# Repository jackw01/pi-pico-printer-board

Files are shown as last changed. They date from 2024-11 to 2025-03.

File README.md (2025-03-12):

# pi-pico-printer-board

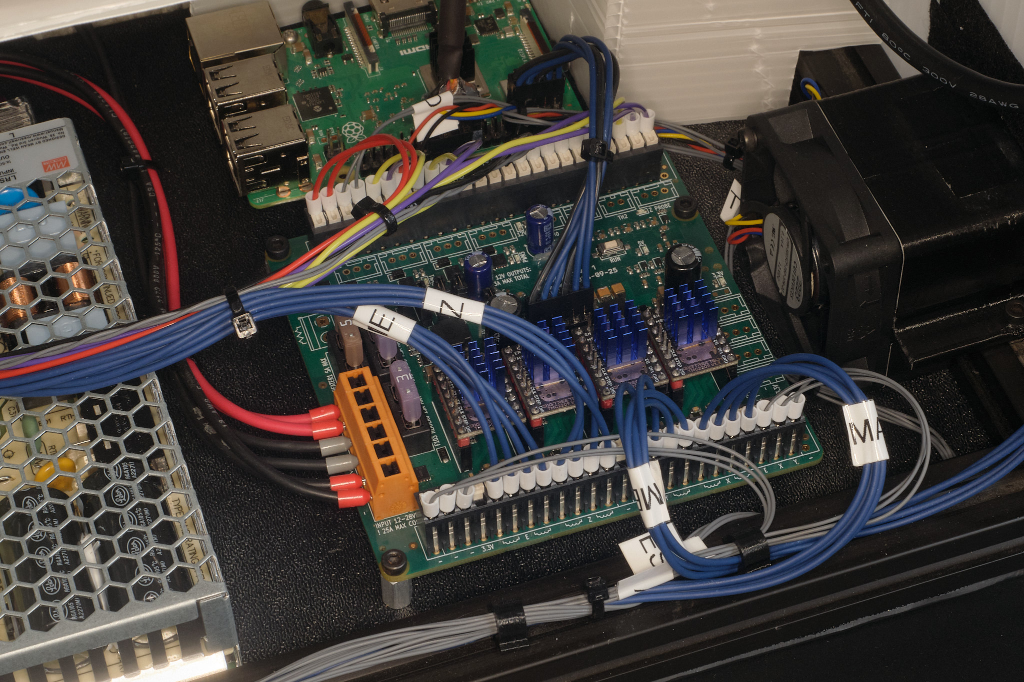
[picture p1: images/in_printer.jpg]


## features

* Klipper compatible
* Uses Raspberry Pi Pico (RP2040)
* High reliability Weidmüller push-in connectors for all inputs and outputs
* 20A max and 7.5A max separately fused heater outputs
* 4x 3A max general purpose PWM outputs, individually configurable for 12V or 24V power, capable of driving inductive loads
* 3x thermistor inputs with 2.4Kohm pull up resistors
* 4x endstop inputs with one configurable for 5V or 12V operation for Z-probe
* 4x motor driver sockets
* Onboard 12V 3A and 5V 3A buck converters for powering accessories including Raspberry Pi
* Compatible with both 12V and 24V systems; components rated for 28V
* Compatible with both TMC2209 and A4988 motor drivers, and possibly others
* ESD and short-to-Vin protection on all microcontroller inputs
* Motor driver ESD and coil overvoltage protection
* Indicator LEDs for all power rails and outputs
* Alternatively supports 2.54mm pitch (Molex SL), or 2.5mm pitch (JST SM) headers for all inputs and outputs
* Labeled PCB for ease of setup and tinkering
* Open source PCB design

## design

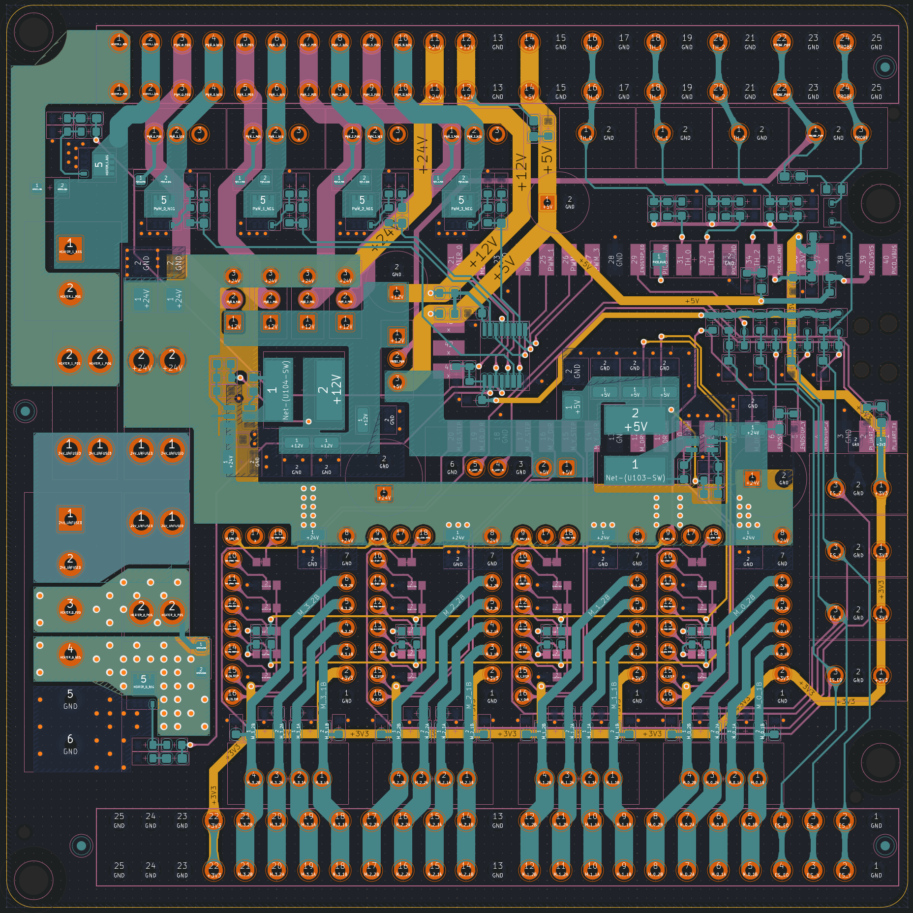
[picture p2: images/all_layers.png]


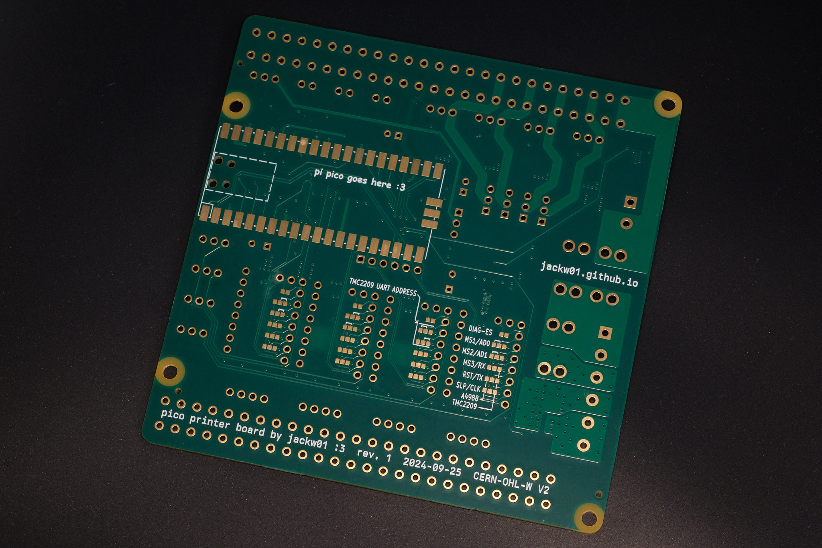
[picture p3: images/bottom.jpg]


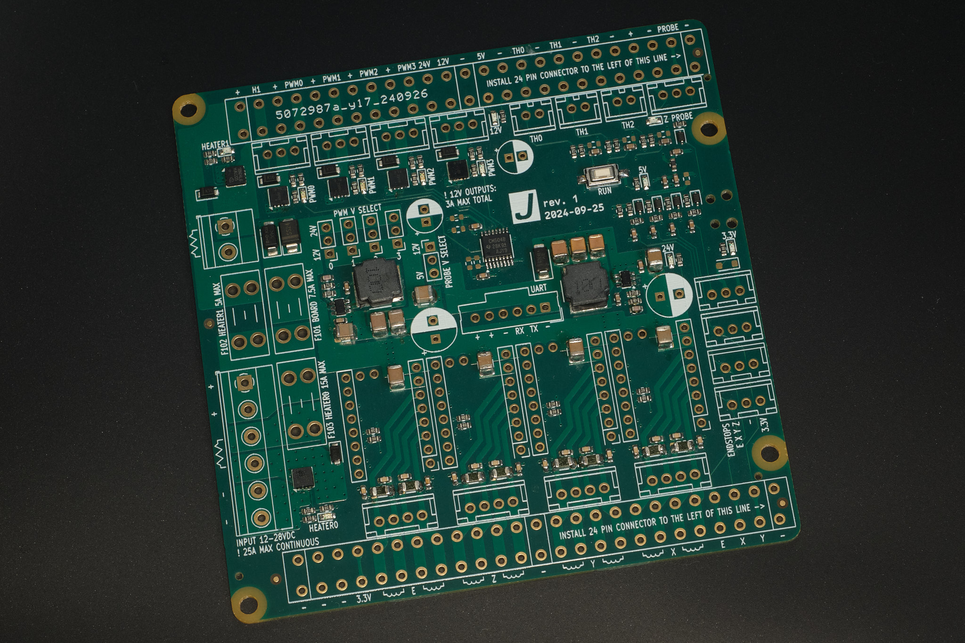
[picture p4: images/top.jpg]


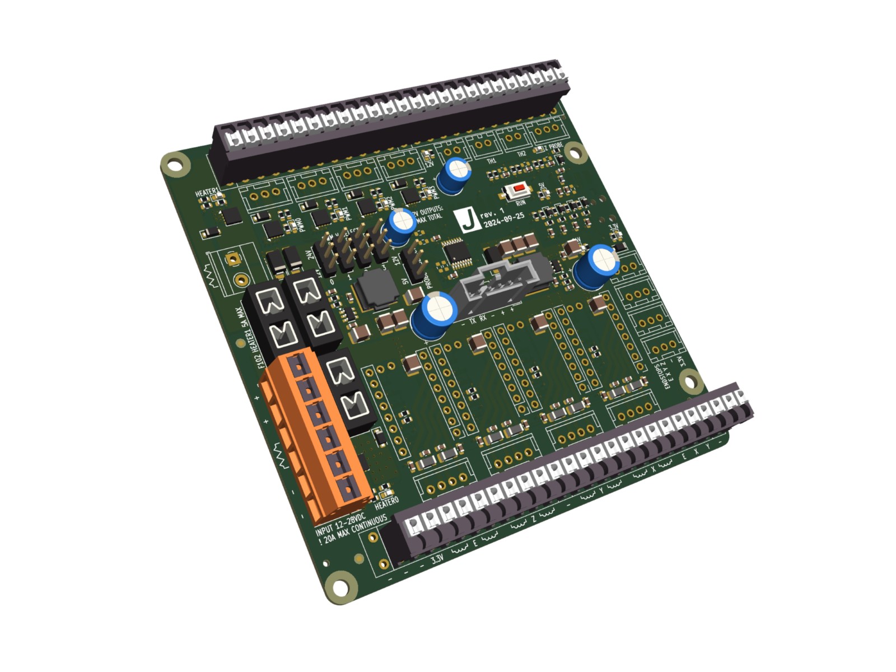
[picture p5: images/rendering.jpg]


[Schematic as PDF](pcb/rpi%20pico%20printer%20board%20rev1%2020241010.pdf)

[Sample Klipper Configuration File](klipper/printer.cfg)

[BOM (Excel)](pcb/bom.xlsx)

### license
This project is released under the CERN Open Hardware Licence Version 2 - Weakly Reciprocal (CERN-OHL-W V2).

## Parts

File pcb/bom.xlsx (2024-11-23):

 |  |  |  |  | 168 | 25 |  |  |  |  | $48.15 |  |  | $123.98
Reference | Value | Datasheet | Footprint | SMT | Qty | Qty THT | DNP | MPN | JLCPCB Basic/ExtPref | Cost | Ext. Cost Per Board | MOQ | Already Have? | Order Cost
A201,A301,A401,A501 | Stepper Driver Breakout | ~ | Custom:BTT_TMC2209_Breakout-16_15.2x20.3mm |  | 8 | 8 |  | RS1-08-G |  | 0.43 | 3.44 | 17 |  | 7.31
C101,C102,C104,C109,C116,C118,C125,C127,C128,C129,C130 | 0.1u | ~ | Capacitor_SMD:C_0603_1608Metric | Y | 11 | 0 |  | CL10B104KB8NNWC | CC0603KRX7R9BB104 | 0.0079 | 0.0869 | 100 |  | 0
C103,C105,C106,C108,C117 | 2.2u | ~ | Capacitor_SMD:C_0603_1608Metric | Y | 5 | 0 |  | CL10B225KP8NNNC | CL10A225KO8NNNC | 0.041 | 0.205 | 50 |  | 0
C107,C126 | 470u | ~ | Capacitor_THT:CP_Radial_D8.0mm_P3.50mm |  | 2 | 2 |  | EEU-FR1V471L |  | 0.451 | 0.902 | 10 |  | 4.51
C110 | 47p | ~ | Capacitor_SMD:C_0603_1608Metric | Y | 1 | 0 |  | CL10C470JB8NNNC | CL10C470JB8NNNC | 0.034 | 0.034 | 10 |  | 0
C111,C112,C113 | 22u | ~ | Capacitor_SMD:C_1210_3225Metric | Y | 3 | 0 |  | CL32B226KOJNNNE |  | 0.295 | 0.885 | 10 |  | 2.95
C114,C123 | 100u | ~ | Capacitor_THT:CP_Radial_D6.3mm_P2.50mm |  | 2 | 2 |  | ECA-1VM101 |  | 0.19 | 0.38 | 10 |  | 1.9
C115,C120,C121,C122,C124,C201,C301,C401,C501 | 10u | ~ | Capacitor_SMD:C_1210_3225Metric | Y | 9 | 0 |  | CL32B106KBJNNNE |  | 0.2806 | 2.5254 | 50 |  | 14.03
C119 | 12p | ~ | Capacitor_SMD:C_0603_1608Metric | Y | 1 | 0 |  | CL10C120JB8NNNC | CL10C120JB8NNNC | 0.022 | 0.022 | 10 |  | 0
C203,C204,C205,C206,C303,C304,C305,C306,C403,C404,C405,C406,C503,C504,C505,C506 | 1n | ~ | Capacitor_SMD:C_0603_1608Metric | Y | 16 | 0 |  | CL10B102KB8NNNC | CL10B102KB8NNNC | 0.0122 | 0.1952 | 100 |  | 0
D101,D102,D106,D107,D108,D112,D113,D114,D118,D120,D123 | LED | ~ | LED_SMD:LED_0603_1608Metric_Pad1.05x0.95mm_HandSolder | Y | 11 | 0 |  | B1911UD--20D001014U1930 | KT-0603R | 0.047 | 0.517 | 10 |  | 0
D103,D104,D105,D109,D110,D111 | DSS16U | ~ | Diode_SMD:D_SOD-123 | Y | 6 | 0 |  | DSS16U | DSK16 | 0.119 | 0.714 | 10 |  | 0
D115 | D3V3AP2W | ~ | Diode_SMD:D_SOD-123 | Y | 1 | 0 |  | GSMF3.3CA |  | 0.134 | 0.134 | 10 |  | 1.34
D116 | SMAJ30A | ~ | Diode_SMD:D_SMA | Y | 1 | 0 |  | SMAJ30A | SMAJ30CA | 0.39 | 0.39 | 1 |  | 0
D117 | SMAJ5.0A | ~ | Diode_SMD:D_SMA | Y | 1 | 0 |  | SMAJ5.0A | SMAJ5.0A | 0.39 | 0.39 | 1 |  | 0
D119,D121,D122,D124,D125 | BAT46WS | ~ | Diode_SMD:D_SOD-323 | Y | 5 | 0 |  | BAT46WS | BAT46WS | 0.139 | 0.695 | 10 |  | 0
D126 | SS24 | ~ | Diode_SMD:D_SMA | Y | 1 | 0 |  | SS24 | SS24 | 0.267 | 0.267 | 10 |  | 0
F101 | 5A | ~ | Fuse:Fuseholder_Blade_Mini_Keystone_3568 |  | 1 | 1 |  | 3568 |  | 1.31 | 1.31 | 1 |  | 2.62
F102 | 7.5A | ~ | Fuse:Fuseholder_Blade_Mini_Keystone_3568 |  | 1 | 1 |  | 3568 |  | 1.31 | 1.31 | 1 |  | 2.62
F103 | 15A | ~ | Fuse:Fuseholder_Blade_Mini_Keystone_3568 |  | 1 | 1 |  | 3568 |  | 1.31 | 1.31 | 1 |  | 2.62
FB101 | 600ohm@100MHz | ~ | Inductor_SMD:L_0603_1608Metric | Y | 1 | 0 |  | BLM18AG601SH1D | GZ1608D601TF | 0.071 | 0.071 | 10 |  | 0
J101,J102,J105,J106,J120 | 2.54mm | ~ | Connector_PinHeader_2.54mm:PinHeader_1x03_P2.54mm_Vertical |  | 5 | 5 |  | PH1-03-UA |  | 0.047 | 0.235 | 10 |  | 0.47
J109,J110 | Conn_01x25 | ~ | Custom:Weidmuller_1870890000_25 |  | 2 | 2 |  | 1870630000 |  | 5.55 | 11.1 | 1 |  | 22.2
J113 | UART | ~ | Custom:Molex_SL_171971-0006_1x06_P2.54mm_Vertical |  | 1 | 1 |  | 1719710006 |  | 1.43 | 1.43 | 1 |  | 2.86
J114 | Screw_Terminal_01x06 | ~ | Custom:Weidmuller_LMFV_5.00_06_90 |  | 1 | 1 |  | 2786570000 |  | 4.26 | 4.26 | 1 |  | 8.52
L101,L102 | 10uH | ~ | Custom:L_Bourns_SRN8040TA | Y | 2 | 0 |  | SRN8040TA-100M |  | 0.552 | 1.104 | 10 |  | 5.52
Q101,Q104 | BSZ021N04 |  | Package_SON:Diodes_PowerDI3333-8 | Y | 2 | 0 |  | BSZ021N04LS6ATMA1 |  | 1.566 | 3.132 | 10 |  | 15.66
Q102,Q103,Q105,Q106 | DMT4011LFG |  | Package_SON:Diodes_PowerDI3333-8 | Y | 4 | 0 |  | DMT4011LFG-13 |  | 0.442 | 1.768 | 10 |  | 4.42
R101,R109,R110,R111,R119,R120,R121 | 22k | ~ | Resistor_SMD:R_0603_1608Metric | Y | 7 | 0 |  |  | 0603WAF2202T5E | 0.0078 | 0.0546 | 50 |  | 0
R102,R125,R129,R137 | 2.49k | ~ | Resistor_SMD:R_0603_1608Metric | Y | 4 | 0 |  |  | 0603WAF2401T5E | 0.0078 | 0.0312 | 50 |  | 0
R104,R112,R113,R114,R122,R123,R124,R126,R128,R130,R131,R132,R134,R135,R136,R139,R140,R141,R145,R149 | 10k | ~ | Resistor_SMD:R_0603_1608Metric | Y | 20 | 0 |  |  | 0603WAF1002T5E | 0.0078 | 0.156 | 50 |  | 0
R105,R106,R107,R116,R117,R118,R150,R202,R302,R402,R502 | 1k | ~ | Resistor_SMD:R_0603_1608Metric | Y | 11 | 0 |  |  | 0603WAF1001T5E | 0.0078 | 0.0858 | 50 |  | 0
R138 | 172k | ~ | Resistor_SMD:R_0603_1608Metric | Y | 1 | 0 |  |  | 0603WAF1803T5E | 0.0078 | 0.0078 | 50 |  | 0
R143,R146 | 31.6k | ~ | Resistor_SMD:R_0603_1608Metric | Y | 2 | 0 |  |  | 0603WAF3302T5E | 0.0078 | 0.0156 | 50 |  | 0
R144 | 475k | ~ | Resistor_SMD:R_0603_1608Metric | Y | 1 | 0 |  |  | 0603WAF4703T5E | 0.0078 | 0.0078 | 50 |  | 0
R201,R301,R401,R501 | 100 | ~ | Resistor_SMD:R_0603_1608Metric | Y | 4 | 0 |  |  | 0603WAF1000T5E | 0.0078 | 0.0312 | 50 |  | 0
RV201,RV202,RV301,RV302,RV401,RV402,RV501,RV502 | 26V | ~ | Inductor_SMD:L_1206_3216Metric | Y | 8 | 0 |  | ZV25K1206201NIR1 |  | 0.298 | 2.384 | 25 |  | 7.45
SW101 | PTS636 SM25 SMTR LFS | ~ | Button_Switch_SMD:SW_SPST_CK_RS282G05A3 | Y | 1 | 0 |  | PTS636 SM25 SMTR LFS |  | 0.24 | 0.24 | 1 |  | 0.48
U101 | 4504 | ~ | Package_SO:TSSOP-16_4.4x5mm_P0.65mm | Y | 1 | 0 |  | CD4504BPWR |  | 0.482 | 0.482 | 10 |  | 4.82
U102 | Raspberry Pi Pico | ~ | Custom:RPi_Pico_SMD_minimal |  | 1 | 1 |  | SC0915 |  | 4 | 4 | 1 |  | 8
U103,U104 | AP63300WU | https://www.diodes.com/assets/Datasheets/AP63300-AP63301.pdf | Package_TO_SOT_SMD:TSOT-23-6 | Y | 2 | 0 |  | AP63300WU-7 |  | 0.92 | 1.84 | 1 |  | 3.68

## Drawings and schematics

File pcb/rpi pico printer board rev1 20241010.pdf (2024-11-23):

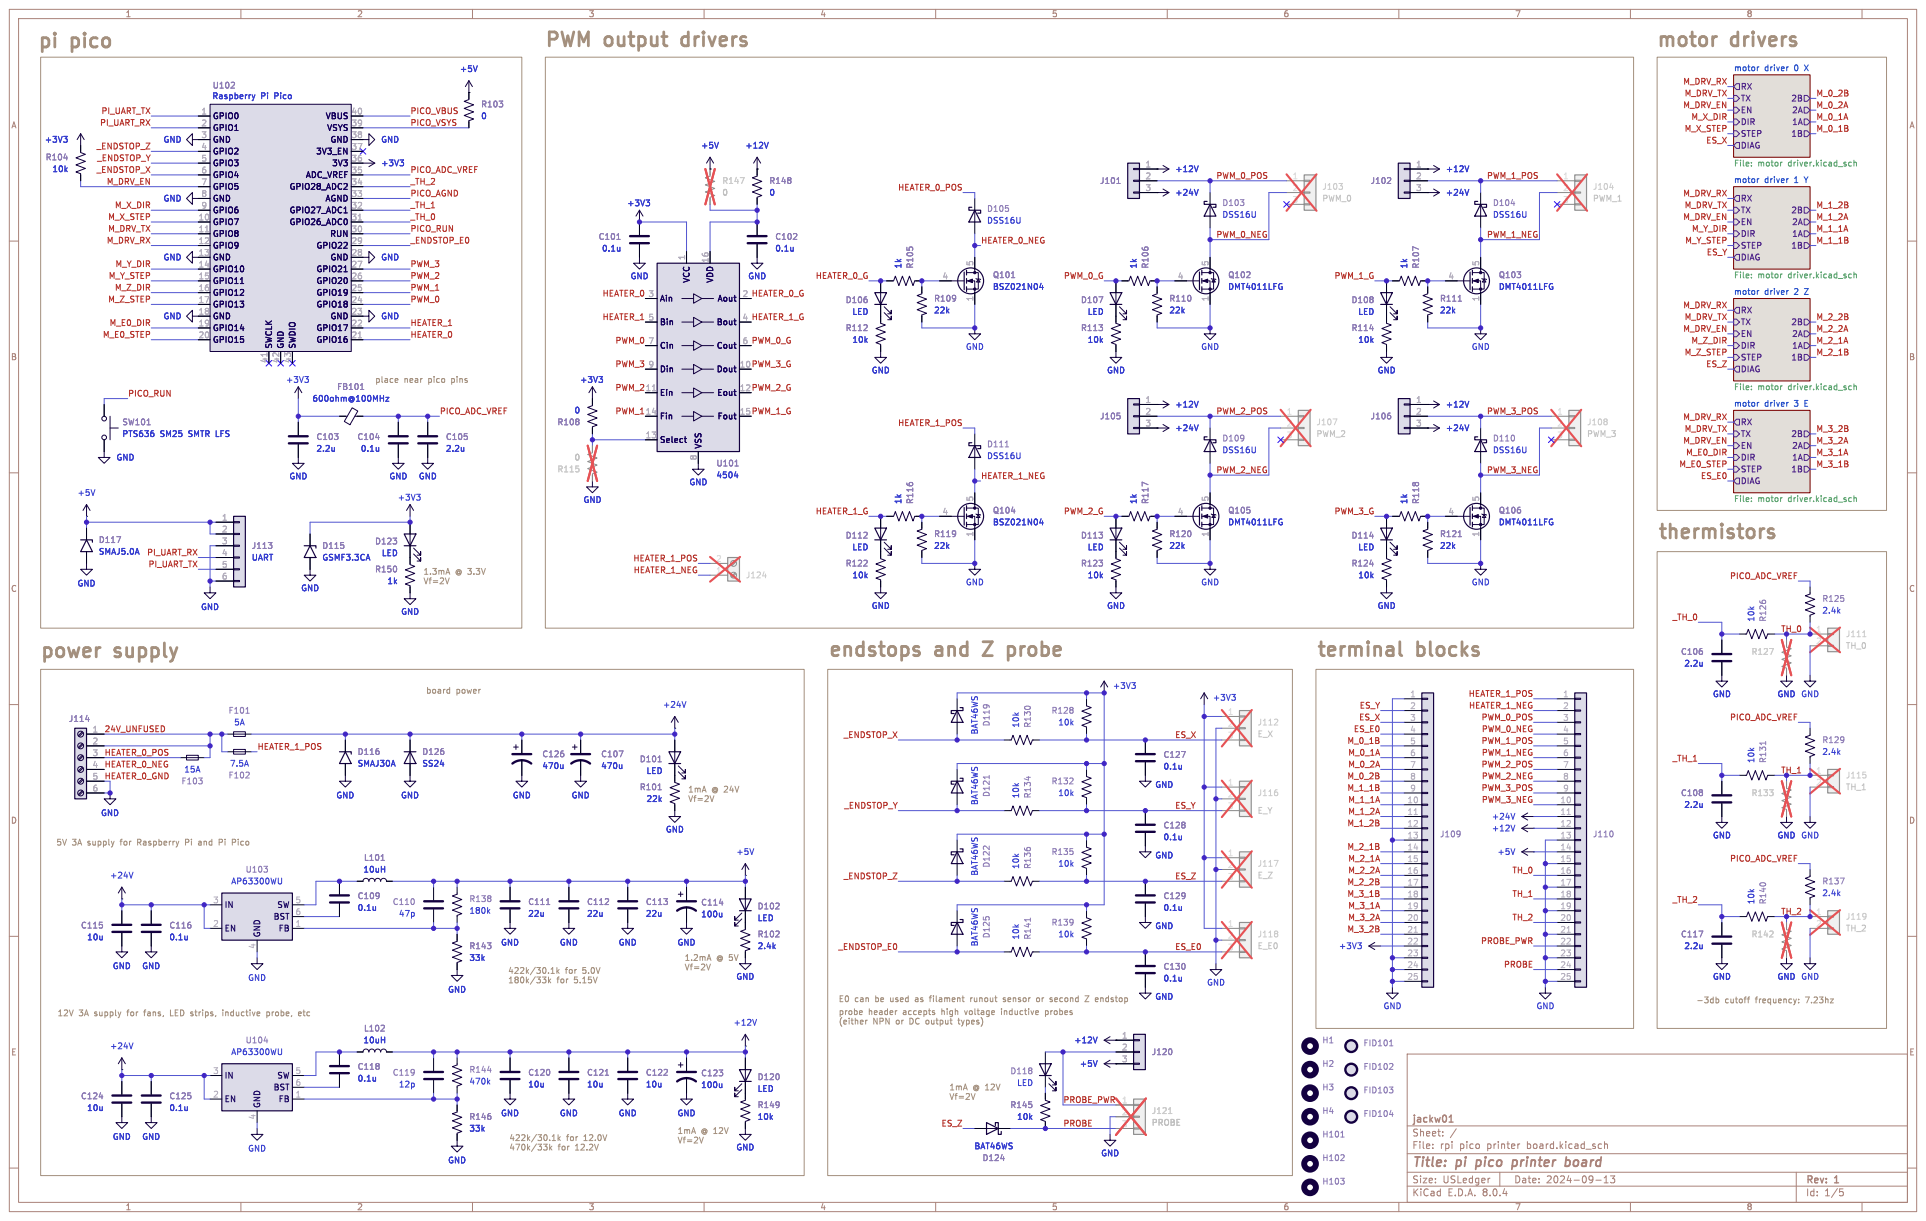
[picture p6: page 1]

STEP
DIAG
File: motor driver.kicad_sch DIR
2B motor driver 2 Z

1 Dout 10 Ein 11 Eout 12 Select 13 Fin 14 Fout 15 VDD 16 Aout 2 Ain 3 Bout 4 Bin 5 Cout 6 Cin 7 VSS
GND

2B motor driver 3 E

place near pico pins

5V 3A supply for Raspberry Pi and Pi Pico

(either NPN or DC output types)

jackw01
Id: 1/5 Title: pi pico printer board

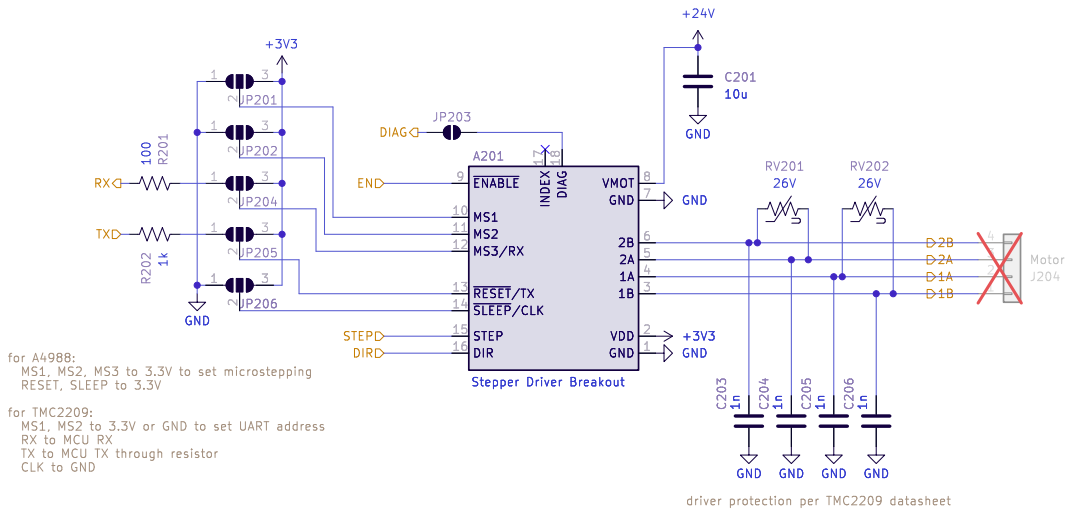
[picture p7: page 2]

J204 Motor +3V3 GND GND GND

for A4988: MS1, MS2, MS3 to 3.3V to set microstepping RESET, SLEEP to 3.3V

for TMC2209: MS1, MS2 to 3.3V or GND to set UART address RX to MCU RX

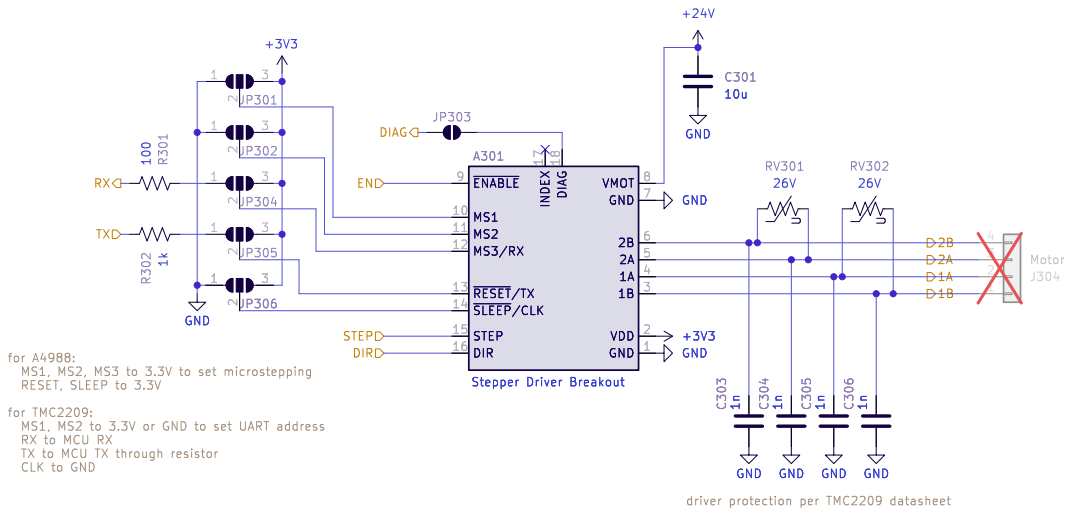
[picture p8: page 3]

for A4988: MS1, MS2, MS3 to 3.3V to set microstepping RESET, SLEEP to 3.3V

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

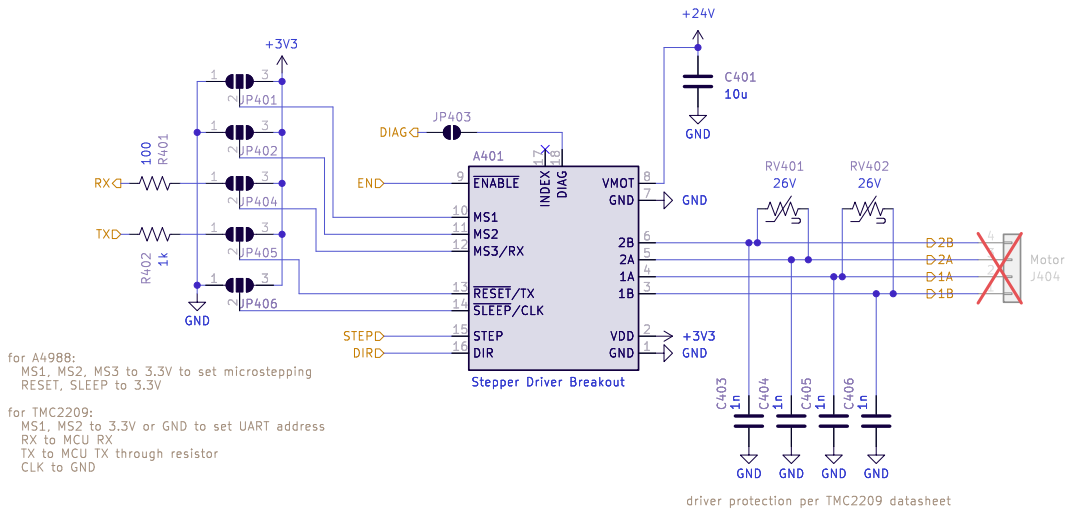
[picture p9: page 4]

for A4988: MS1, MS2, MS3 to 3.3V to set microstepping RESET, SLEEP to 3.3V

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

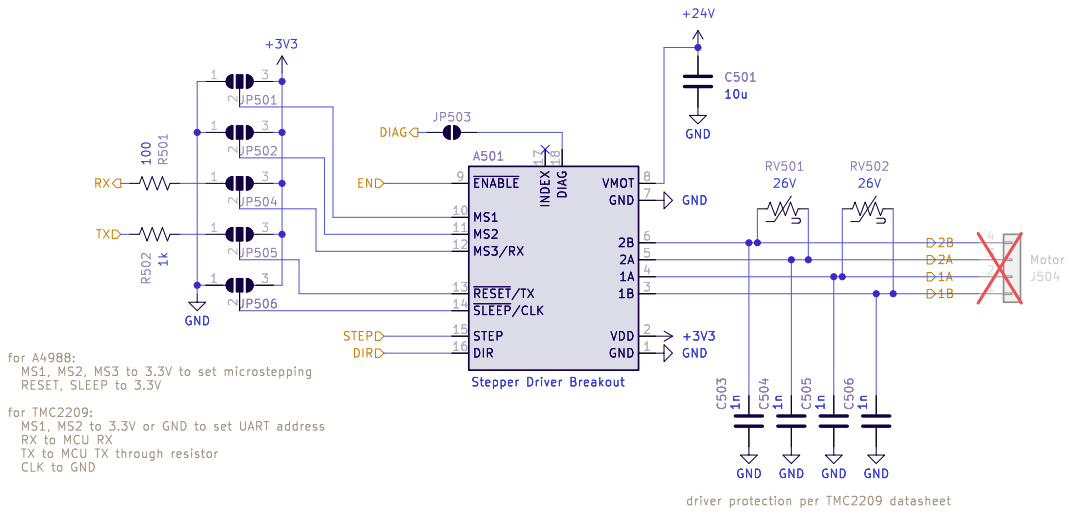
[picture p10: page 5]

J504 Motor +3V3 GND GND GND

for A4988: MS1, MS2, MS3 to 3.3V to set microstepping RESET, SLEEP to 3.3V

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

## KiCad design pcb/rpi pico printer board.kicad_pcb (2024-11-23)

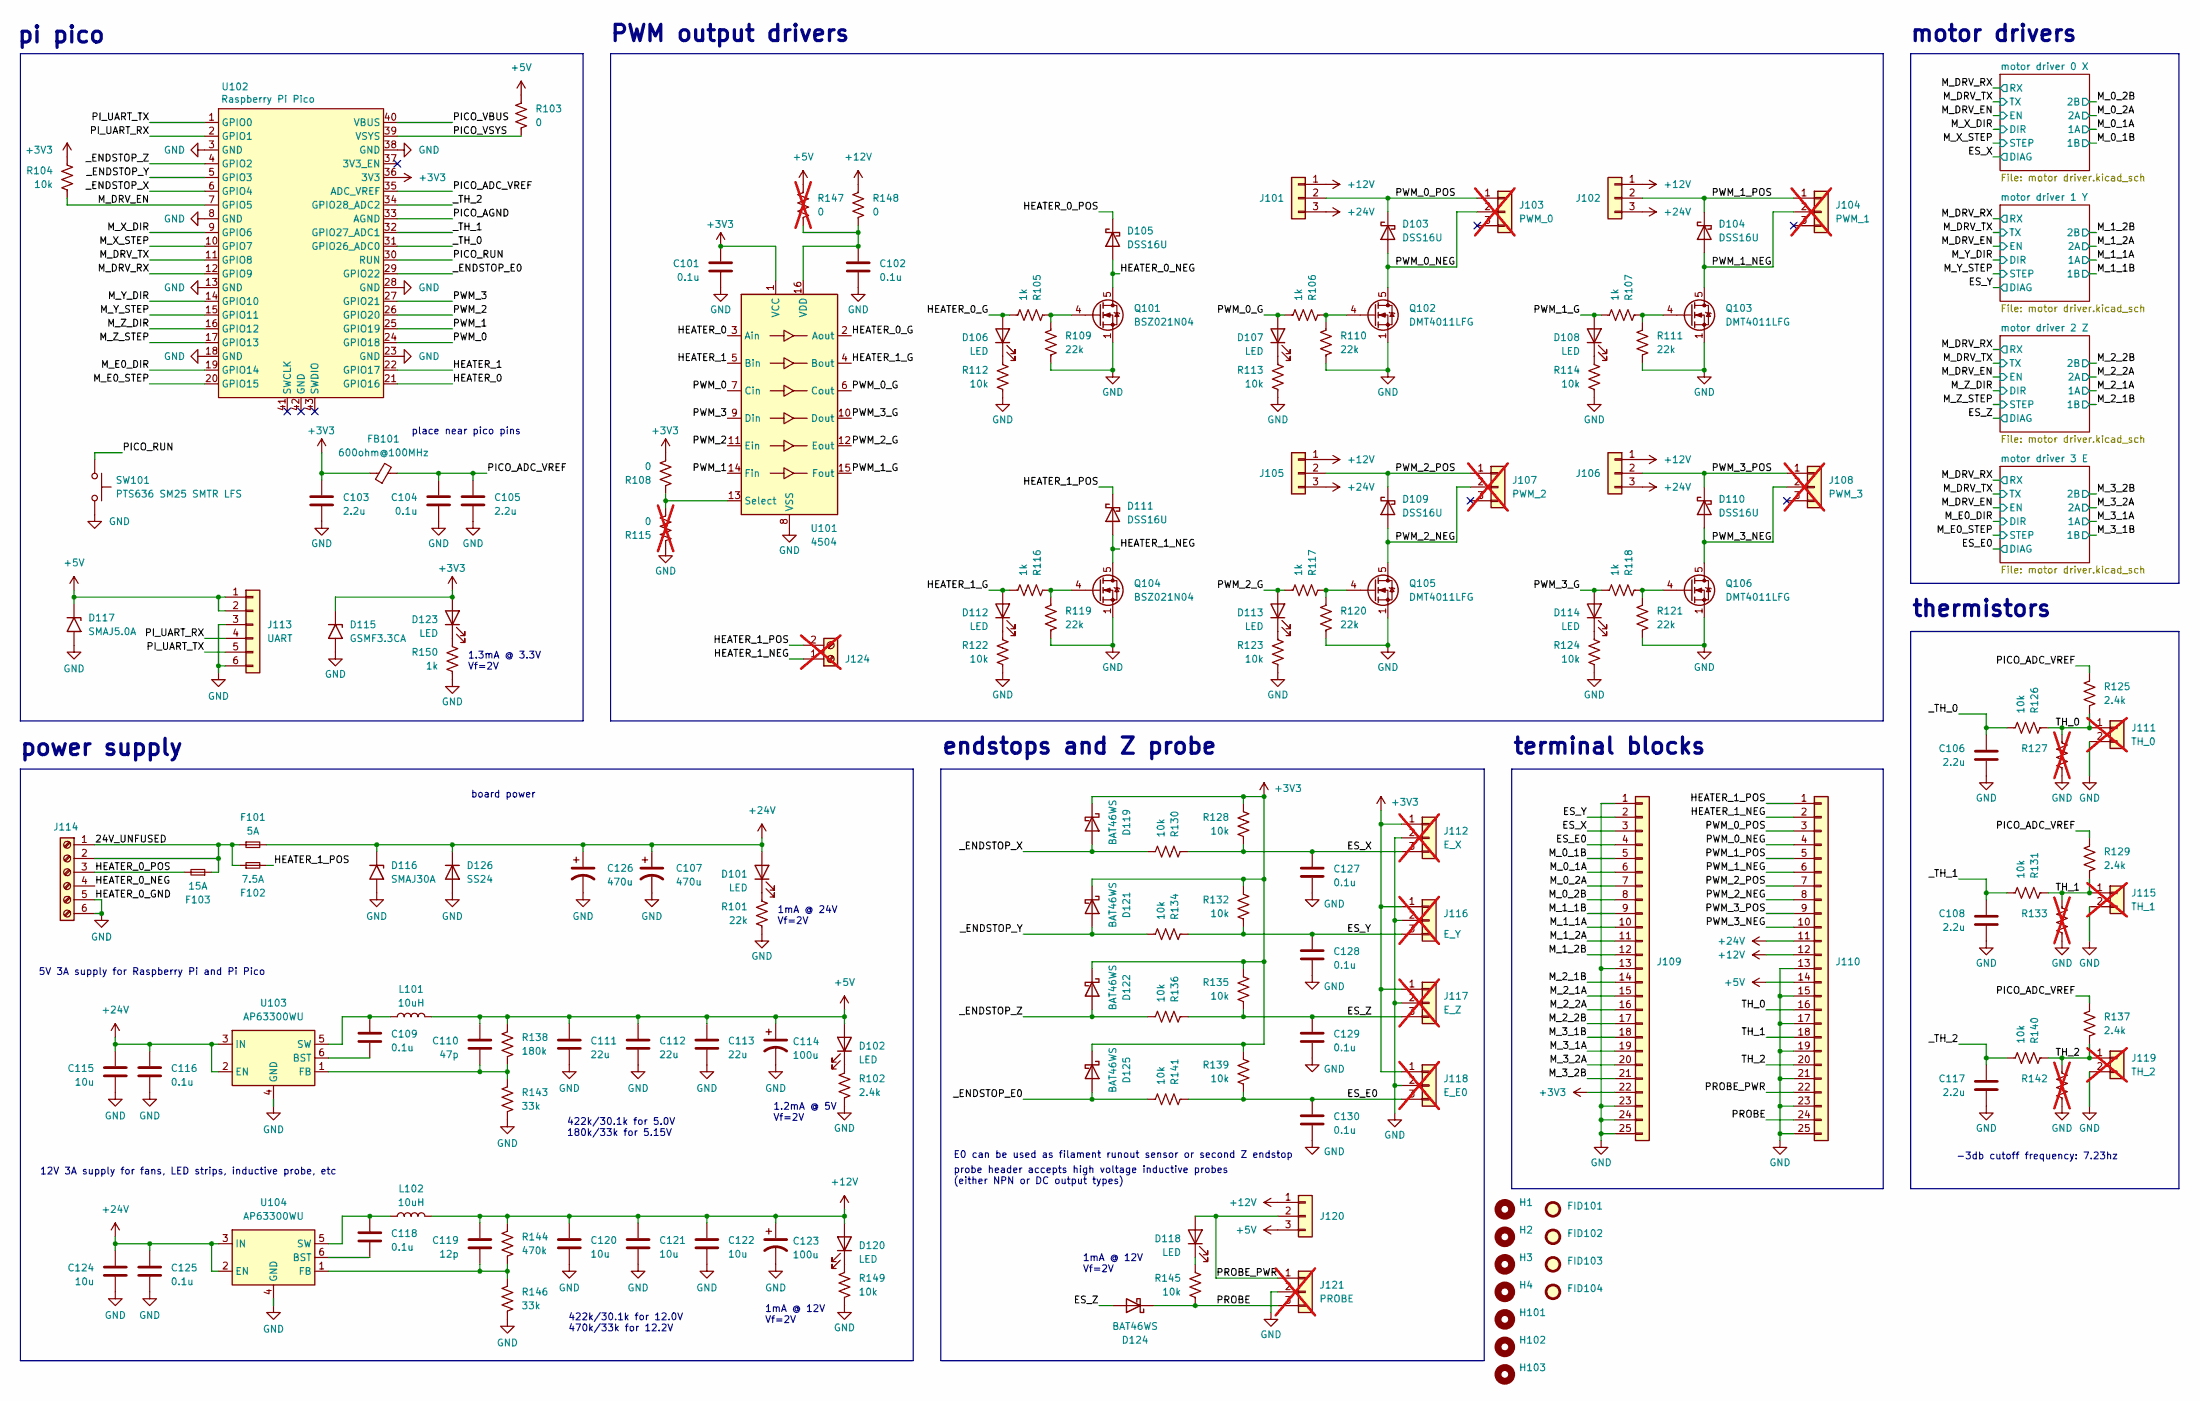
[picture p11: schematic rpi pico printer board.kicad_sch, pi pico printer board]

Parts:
C101, C102, C104, C109, C116, C118, C125, C127, C128, C129, C130: 0.1u; C_0603_1608Metric; MPN CL10B104KB8NNWC; JLCPCB Basic Part CC0603KRX7R9BB104
C103, C105, C106, C108, C117: 2.2u; C_0603_1608Metric; MPN CL10B225KP8NNNC; JLCPCB Basic Part CL10A225KO8NNNC
C107, C126: 470u; CP_Radial_D8.0mm_P3.50mm; MPN EEU-FR1V471L
C110: 47p; C_0603_1608Metric; MPN CL10C470JB8NNNC; JLCPCB Basic Part CL10C470JB8NNNC
C111, C112, C113: 22u; C_1210_3225Metric; MPN CL32B226KOJNNNE
C114, C123: 100u; CP_Radial_D6.3mm_P2.50mm; MPN ECA-1VM101
C115, C120, C121, C122, C124: 10u; C_1210_3225Metric; MPN CL32B106KBJNNNE
C119: 12p; C_0603_1608Metric; MPN CL10C120JB8NNNC; JLCPCB Basic Part CL10C120JB8NNNC
D101, D102, D106, D107, D108, D112, D113, D114, D118, D120, D123: LED; LED_0603_1608Metric_Pad1.05x0.95mm_HandSolder; MPN B1911UD--20D001014U1930; JLCPCB Basic Part KT-0603R
D103, D104, D105, D109, D110, D111: DSS16U; D_SOD-123F; MPN DSS16U; JLCPCB Basic Part DSK16
D115: GSMF3.3CA; D_SOD-123F; MPN GSMF3.3CA; JLCPCB Basic Part SMF3.3CA
D116: SMAJ30A; D_SMA; MPN SMAJ30A; JLCPCB Basic Part SMAJ30CA
D117: SMAJ5.0A; D_SMA; MPN SMAJ5.0A; JLCPCB Basic Part SMAJ5.0A
D119, D121, D122, D124, D125: BAT46WS; D_SOD-323; MPN BAT46WS; JLCPCB Basic Part BAT46WS
D126: SS24; D_SMA; MPN SS24; JLCPCB Basic Part SS24
F101: 5A; Fuseholder_Blade_Mini_Keystone_3568; MPN 3568
F102: 7.5A; Fuseholder_Blade_Mini_Keystone_3568; MPN 3568
F103: 15A; Fuseholder_Blade_Mini_Keystone_3568; MPN 3568
FB101: 600ohm@100MHz; L_0603_1608Metric; MPN BLM18AG601SH1D; JLCPCB Basic Part GZ1608D601TF
FID101, FID102, FID103, FID104: Fiducial_1mm_Mask2mm
H1, H2, H3, H4: MountingHole; MountingHole_3.2mm_M3_Mask
H101, H102, H103: ToolingHole; JLC_tooling_hole
J101, J102, J105, J106, J120: 2.54mm; PinHeader_1x03_P2.54mm_Vertical; MPN PH1-03-UA
J103: PWM_0; JST_XH_plus_2.54mm_01x03; not fitted
J104: PWM_1; JST_XH_plus_2.54mm_01x03; not fitted
J107: PWM_2; JST_XH_plus_2.54mm_01x03; not fitted
J108: PWM_3; JST_XH_plus_2.54mm_01x03; not fitted
J109, J110: Conn_01x25; Weidmuller_1870890000_25; MPN 1870630000
J111: TH_0; JST_XH_plus_2.54mm_01x02; not fitted
J112: E_X; JST_XH_plus_2.54mm_01x03; not fitted
J113: UART; Molex_SL_171971-0006_1x06_P2.54mm_Vertical; MPN 1719710006
J114: Screw_Terminal_01x06; Weidmuller_LMFV_5.00_06_90; MPN 2786570000
J115: TH_1; JST_XH_plus_2.54mm_01x02; not fitted
J116: E_Y; JST_XH_plus_2.54mm_01x03; not fitted
J117: E_Z; JST_XH_plus_2.54mm_01x03; not fitted
J118: E_E0; JST_XH_plus_2.54mm_01x03; not fitted
J119: TH_2; JST_XH_plus_2.54mm_01x02; not fitted
J121: PROBE; JST_XH_plus_2.54mm_01x03; not fitted
J124: Screw_Terminal_01x02; TerminalBlock_Phoenix_MKDS-1,5-2_1x02_P5.00mm_Horizontal; not fitted
L101, L102: 10uH; L_Bourns_SRN8040TA; MPN SRN8040TA-100M
Q101, Q104: BSZ021N04; Diodes_PowerDI3333-8; MPN BSZ021N04LS6ATMA1
Q102, Q103, Q105, Q106: DMT4011LFG; Diodes_PowerDI3333-8; MPN DMT4011LFG-13
R101, R109, R110, R111, R119, R120, R121: 22k; R_0603_1608Metric; JLCPCB Basic Part 0603WAF2202T5E
R102, R125, R129, R137: 2.4k; R_0603_1608Metric; JLCPCB Basic Part 0603WAF2401T5E
R103, R108, R148: 0; R_0603_1608Metric_Bridged
R104, R112, R113, R114, R122, R123, R124, R126, R128, R130, R131, R132, R134, R135, R136, R139, R140, R141, R145, R149: 10k; R_0603_1608Metric; JLCPCB Basic Part 0603WAF1002T5E
R105, R106, R107, R116, R117, R118, R150: 1k; R_0603_1608Metric; JLCPCB Basic Part 0603WAF1001T5E
R115, R147: 0; R_0603_1608Metric; not fitted
R127, R133, R142: R_0603_1608Metric; not fitted
R138: 180k; R_0603_1608Metric; JLCPCB Basic Part 0603WAF1803T5E
R143, R146: 33k; R_0603_1608Metric; JLCPCB Basic Part 0603WAF3302T5E
R144: 470k; R_0603_1608Metric; JLCPCB Basic Part 0603WAF4703T5E
SW101: PTS636 SM25 SMTR LFS; SW_SPST_CK_RS282G05A3; MPN PTS636 SM25 SMTR LFS
U101: 4504; TSSOP-16_4.4x5mm_P0.65mm; MPN CD4504BPWR
U102: Raspberry Pi Pico; RPi_Pico_SMD_minimal; MPN SC0915
U103, U104: AP63300WU; TSOT-23-6; MPN AP63300WU-7

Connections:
+3V3: C101.1, C103.1, D115.1 (A1), D119.1 (K), D121.1 (K), D122.1 (K), D123.2 (A), D125.1 (K), FB101.1, J109.22, J112.1, J116.1, J117.1, J118.1, R104.1, R108.2, R128.1, R132.1, R135.1, R139.1, U101.1 (VCC), U102.36 (3V3); also elsewhere on the board
+5V: C110.1, C111.1, C112.1, C113.1, C114.1, D102.2 (A), D117.1 (A1), J110.14, J113.1, J113.2, J120.3, L101.2, R103.1, R138.1, R147.1
+12V: C119.1, C120.1, C121.1, C122.1, C123.1, D120.2 (A), J101.1, J102.1, J105.1, J106.1, J110.12, J120.1, L102.2, R144.1, R148.1
+24V: C107.1, C115.1, C116.1, C124.1, C125.1, C126.1, D101.2 (A), D116.1 (A1), D126.1 (K), F101.2, J101.3, J102.3, J105.3, J106.3, J110.11, U103.2 (EN), U103.3 (IN), U104.2 (EN), U104.3 (IN); also elsewhere on the board
/24V_UNFUSED: F101.1, F102.1, F103.1, J114.1, J114.2
/ES_E0: C130.1, J109.4, J118.3, R139.2, R141.1; also elsewhere on the board
/ES_X: C127.1, J109.3, J112.3, R128.2, R130.1; also elsewhere on the board
/ES_Y: C128.1, J109.2, J116.3, R132.2, R134.1; also elsewhere on the board
/ES_Z: C129.1, D124.2 (A), J117.3, R135.2, R136.1; also elsewhere on the board
/HEATER_0: U101.3 (Ain), U102.21 (GPIO16)
/HEATER_0_G: D106.2 (A), R105.2, U101.2 (Aout)
/HEATER_0_NEG: D105.2 (A), J114.4, Q101.5 (D)
/HEATER_0_POS: D105.1 (K), F103.2, J114.3
/HEATER_1: U101.5 (Bin), U102.22 (GPIO17)
/HEATER_1_G: D112.2 (A), R116.2, U101.4 (Bout)
/HEATER_1_NEG: D111.2 (A), J110.2, J124.1, Q104.5 (D)
/HEATER_1_POS: D111.1 (K), F102.2, J110.1, J124.2
/M_0_1A: J109.6; also elsewhere on the board
/M_0_1B: J109.5; also elsewhere on the board
/M_0_2A: J109.7; also elsewhere on the board
/M_0_2B: J109.8; also elsewhere on the board
/M_1_1A: J109.10; also elsewhere on the board
/M_1_1B: J109.9; also elsewhere on the board
/M_1_2A: J109.11; also elsewhere on the board
/M_1_2B: J109.12; also elsewhere on the board
/M_2_1A: J109.15; also elsewhere on the board
/M_2_1B: J109.14; also elsewhere on the board
/M_2_2A: J109.16; also elsewhere on the board
/M_2_2B: J109.17; also elsewhere on the board
/M_3_1A: J109.19; also elsewhere on the board
/M_3_1B: J109.18; also elsewhere on the board
/M_3_2A: J109.20; also elsewhere on the board
/M_3_2B: J109.21; also elsewhere on the board
/M_DRV_EN: R104.2, U102.7 (GPIO5); also elsewhere on the board
/M_DRV_RX: U102.12 (GPIO9); also elsewhere on the board
/M_DRV_TX: U102.11 (GPIO8); also elsewhere on the board
/M_E0_DIR: U102.19 (GPIO14); also elsewhere on the board
/M_E0_STEP: U102.20 (GPIO15); also elsewhere on the board
/M_X_DIR: U102.9 (GPIO6); also elsewhere on the board
/M_X_STEP: U102.10 (GPIO7); also elsewhere on the board
/M_Y_DIR: U102.14 (GPIO10); also elsewhere on the board
/M_Y_STEP: U102.15 (GPIO11); also elsewhere on the board
/M_Z_DIR: U102.16 (GPIO12); also elsewhere on the board
/M_Z_STEP: U102.17 (GPIO13); also elsewhere on the board
/PICO_ADC_VREF: C104.1, C105.1, FB101.2, R125.1, R129.1, R137.1, U102.35 (ADC_VREF)
/PICO_AGND: U102.33 (AGND)
/PICO_RUN: SW101.1, U102.30 (RUN)
/PICO_VBUS: U102.40 (VBUS)
/PICO_VSYS: R103.2, U102.39 (VSYS)
/PI_UART_RX: J113.4, U102.2 (GPIO1)
/PI_UART_TX: J113.5, U102.1 (GPIO0)
/PROBE: D124.1 (K), J110.24, J121.3, R145.2
/PROBE_PWR: D118.2 (A), J110.22, J120.2, J121.1
/PWM_0: U101.7 (Cin), U102.24 (GPIO18)
/PWM_0_G: D107.2 (A), R106.2, U101.6 (Cout)
/PWM_0_NEG: D103.2 (A), J103.2, J110.4, Q102.5 (D)
/PWM_0_POS: D103.1 (K), J101.2, J103.1, J110.3
/PWM_1: U101.14 (Fin), U102.25 (GPIO19)
/PWM_1_G: D108.2 (A), R107.2, U101.15 (Fout)
/PWM_1_NEG: D104.2 (A), J104.2, J110.6, Q103.5 (D)
/PWM_1_POS: D104.1 (K), J102.2, J104.1, J110.5
/PWM_2: U101.11 (Ein), U102.26 (GPIO20)
/PWM_2_G: D113.2 (A), R117.2, U101.12 (Eout)
/PWM_2_NEG: D109.2 (A), J107.2, J110.8, Q105.5 (D)
/PWM_2_POS: D109.1 (K), J105.2, J107.1, J110.7
/PWM_3: U101.9 (Din), U102.27 (GPIO21)
/PWM_3_G: D114.2 (A), R118.2, U101.10 (Dout)
/PWM_3_NEG: D110.2 (A), J108.2, J110.10, Q106.5 (D)
/PWM_3_POS: D110.1 (K), J106.2, J108.1, J110.9
/TH_0: J110.16, J111.1, R125.2, R126.1, R127.1
/TH_1: J110.18, J115.1, R129.2, R131.1, R133.1
/TH_2: J110.20, J119.1, R137.2, R140.1, R142.1
/_ENDSTOP_E0: D125.2 (A), R141.2, U102.29 (GPIO22)
/_ENDSTOP_X: D119.2 (A), R130.2, U102.6 (GPIO4)
/_ENDSTOP_Y: D121.2 (A), R134.2, U102.5 (GPIO3)
/_ENDSTOP_Z: D122.2 (A), R136.2, U102.4 (GPIO2)
/_TH_0: C106.1, R126.2, U102.31 (GPIO26_ADC0)
/_TH_1: C108.1, R131.2, U102.32 (GPIO27_ADC1)
/_TH_2: C117.1, R140.2, U102.34 (GPIO28_ADC2)
GND: C101.2, C102.2, C103.2, C104.2, C105.2, C106.2, C107.2, C108.2, C111.2, C112.2, C113.2, C114.2, C115.2, C116.2, C117.2, C120.2, C121.2, C122.2, C123.2, C124.2, C125.2, C126.2, C127.2, C128.2, C129.2, C130.2, D115.2 (A2), D116.2 (A2), D117.2 (A2), D126.2 (A), J109.1, J109.13, J109.23, J109.24, J109.25, J110.13, J110.15, J110.17, J110.19, J110.21, J110.23, J110.25, J111.2, J112.2, J113.3, J113.6, J114.5, J114.6, J115.2, J116.2, J117.2, J118.2, J119.2, J121.2, Q101.1 (S), Q101.2 (S), Q101.3 (S), Q102.1 (S), Q102.2 (S), Q102.3 (S), Q103.1 (S), Q103.2 (S), Q103.3 (S), Q104.1 (S), Q104.2 (S), Q104.3 (S), Q105.1 (S), Q105.2 (S), Q105.3 (S), Q106.1 (S), Q106.2 (S), Q106.3 (S), R101.2, R102.2, R109.2, R110.2, R111.2, R112.2, R113.2, R114.2, R115.1, R119.2, R120.2, R121.2, R122.2, R123.2, R124.2, R127.2, R133.2, R142.2, R143.2, R146.2, R149.2, R150.2, SW101.2, U101.8 (VSS), U102.3 (GND), U102.8 (GND), U102.13 (GND), U102.18 (GND), U102.23 (GND), U102.28 (GND), U102.38 (GND), U103.4 (GND), U104.4 (GND); also elsewhere on the board
unnamed: D101.1 (K), R101.1
unnamed: D102.1 (K), R102.1
unnamed: D106.1 (K), R112.1
unnamed: D107.1 (K), R113.1
unnamed: D108.1 (K), R114.1
unnamed: D112.1 (K), R122.1
unnamed: D113.1 (K), R123.1
unnamed: D114.1 (K), R124.1
unnamed: D118.1 (K), R145.1
unnamed: D120.1 (K), R149.1
unnamed: D123.1 (K), R150.1
unnamed: Q101.4 (G), R105.1, R109.1
unnamed: Q102.4 (G), R106.1, R110.1
unnamed: Q103.4 (G), R107.1, R111.1
unnamed: Q104.4 (G), R116.1, R119.1
unnamed: Q105.4 (G), R117.1, R120.1
unnamed: Q106.4 (G), R118.1, R121.1
unnamed: R108.1, R115.2, U101.13 (Select)
unnamed: C102.1, R147.2, R148.2, U101.16 (VDD)
unnamed: C109.2, U103.6 (BST)
unnamed: C110.2, R138.2, R143.1, U103.1 (FB)
unnamed: C109.1, L101.1, U103.5 (SW)
unnamed: C118.2, U104.6 (BST)
unnamed: C119.2, R144.2, R146.1, U104.1 (FB)
unnamed: C118.1, L102.1, U104.5 (SW)

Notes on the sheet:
12V 3A supply for fans, LED strips, inductive probe, etc
motor drivers
PWM output drivers
1.2mA @ 5V Vf=2V
E0 can be used as filament runout sensor or second Z endstop
1.3mA @ 3.3V Vf=2V
board power
5V 3A supply for Raspberry Pi and Pi Pico
422k/30.1k for 12.0V 470k/33k for 12.2V
power supply
thermistors
terminal blocks
probe header accepts high voltage inductive probes (either NPN or DC output types)
1mA @ 12V Vf=2V
place near pico pins
1mA @ 24V Vf=2V
-3db cutoff frequency: 7.23hz
pi pico
endstops and Z probe
422k/30.1k for 5.0V 180k/33k for 5.15V

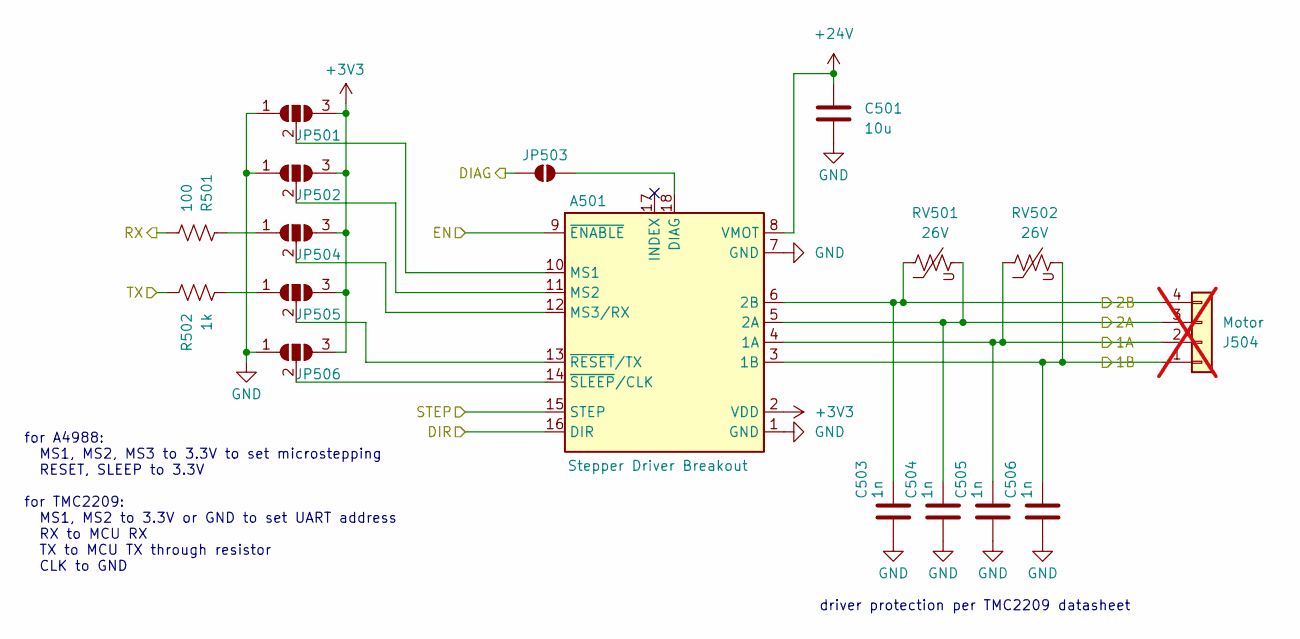
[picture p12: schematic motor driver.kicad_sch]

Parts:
A501: Stepper Driver Breakout; BTT_TMC2209_Breakout-16_15.2x20.3mm; MPN RS1-08-G
C501: 10u; C_1210_3225Metric; MPN CL32B106KBJNNNE
C503, C504, C505, C506: 1n; C_0603_1608Metric; MPN CL10B102KB8NNNC; JLCPCB Basic Part CL10B102KB8NNNC
J504: Motor; JST_XH_plus_2.54mm_01x04; not fitted
JP501, JP502, JP504, JP505, JP506: SolderJumper_3_Open; Bi_0603_Open
JP503: SolderJumper_2_Open; Jumper_0603
R501: 100; R_0603_1608Metric; JLCPCB Basic Part 0603WAF1000T5E
R502: 1k; R_0603_1608Metric; JLCPCB Basic Part 0603WAF1001T5E
RV501, RV502: 26V; L_1206_3216Metric; MPN ZV20K1206201NIR1

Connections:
+3V3: A501.2 (VDD), JP501.3 (B), JP502.3 (B), JP504.3 (B), JP505.3 (B), JP506.3 (B); also elsewhere on the board
+24V: A501.8 (VMOT), C501.1; also elsewhere on the board
/ES_E0: JP503.1 (A); also elsewhere on the board
/M_3_1A: A501.4 (1A), C505.2, J504.2, RV502.1; also elsewhere on the board
/M_3_1B: A501.3 (1B), C506.2, J504.1, RV502.2; also elsewhere on the board
/M_3_2A: A501.5 (2A), C504.2, J504.3, RV501.2; also elsewhere on the board
/M_3_2B: A501.6 (2B), C503.2, J504.4, RV501.1; also elsewhere on the board
/M_DRV_EN: A501.9 (~ENABLE); also elsewhere on the board
/M_DRV_RX: R501.2; also elsewhere on the board
/M_DRV_TX: R502.1; also elsewhere on the board
/M_E0_DIR: A501.16 (DIR); also elsewhere on the board
/M_E0_STEP: A501.15 (STEP); also elsewhere on the board
GND: A501.1 (GND), A501.7 (GND), C501.2, C503.1, C504.1, C505.1, C506.1, JP501.1 (A), JP502.1 (A), JP506.1 (A); also elsewhere on the board
unnamed: A501.18 (DIAG), JP503.2 (B)
unnamed: A501.10 (MS1), JP501.2 (C)
unnamed: A501.11 (MS2), JP502.2 (C)
unnamed: A501.12 (MS3/RX), JP504.2 (C)
unnamed: A501.13 (~RESET/TX), JP505.2 (C)
unnamed: A501.14 (~SLEEP/CLK), JP506.2 (C)
unnamed: JP504.1 (A), R501.1
unnamed: JP505.1 (A), R502.2

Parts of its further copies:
A201, A301, A401: Stepper Driver Breakout; BTT_TMC2209_Breakout-16_15.2x20.3mm; MPN RS1-08-G
C201, C301, C401: 10u; C_1210_3225Metric; MPN CL32B106KBJNNNE
C203, C204, C205, C206, C303, C304, C305, C306, C403, C404, C405, C406: 1n; C_0603_1608Metric; MPN CL10B102KB8NNNC; JLCPCB Basic Part CL10B102KB8NNNC
J204, J304, J404: Motor; JST_XH_plus_2.54mm_01x04; not fitted
JP201, JP202, JP204, JP205, JP206, JP301, JP302, JP304, JP305, JP306, JP401, JP402, JP404, JP405, JP406: SolderJumper_3_Open; Bi_0603_Open
JP203, JP303, JP403: SolderJumper_2_Open; Jumper_0603
R201, R301, R401: 100; R_0603_1608Metric; JLCPCB Basic Part 0603WAF1000T5E
R202, R302, R402: 1k; R_0603_1608Metric; JLCPCB Basic Part 0603WAF1001T5E
RV201, RV202, RV301, RV302, RV401, RV402: 26V; L_1206_3216Metric; MPN ZV20K1206201NIR1

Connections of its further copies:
+3V3: A201.2 (VDD), A301.2 (VDD), A401.2 (VDD), JP201.3 (B), JP202.3 (B), JP204.3 (B), JP205.3 (B), JP206.3 (B), JP301.3 (B), JP302.3 (B), JP304.3 (B), JP305.3 (B), JP306.3 (B), JP401.3 (B), JP402.3 (B), JP404.3 (B), JP405.3 (B), JP406.3 (B); also elsewhere on the board
+24V: A201.8 (VMOT), A301.8 (VMOT), A401.8 (VMOT), C201.1, C301.1, C401.1; also elsewhere on the board
/ES_X: JP203.1 (A); also elsewhere on the board
/ES_Y: JP303.1 (A); also elsewhere on the board
/ES_Z: JP403.1 (A); also elsewhere on the board
/M_0_1A: A201.4 (1A), C205.2, J204.2, RV202.1; also elsewhere on the board
/M_0_1B: A201.3 (1B), C206.2, J204.1, RV202.2; also elsewhere on the board
/M_0_2A: A201.5 (2A), C204.2, J204.3, RV201.2; also elsewhere on the board
/M_0_2B: A201.6 (2B), C203.2, J204.4, RV201.1; also elsewhere on the board
/M_1_1A: A301.4 (1A), C305.2, J304.2, RV302.1; also elsewhere on the board
/M_1_1B: A301.3 (1B), C306.2, J304.1, RV302.2; also elsewhere on the board
/M_1_2A: A301.5 (2A), C304.2, J304.3, RV301.2; also elsewhere on the board
/M_1_2B: A301.6 (2B), C303.2, J304.4, RV301.1; also elsewhere on the board
/M_2_1A: A401.4 (1A), C405.2, J404.2, RV402.1; also elsewhere on the board
/M_2_1B: A401.3 (1B), C406.2, J404.1, RV402.2; also elsewhere on the board
/M_2_2A: A401.5 (2A), C404.2, J404.3, RV401.2; also elsewhere on the board
/M_2_2B: A401.6 (2B), C403.2, J404.4, RV401.1; also elsewhere on the board
/M_DRV_EN: A201.9 (~ENABLE), A301.9 (~ENABLE), A401.9 (~ENABLE); also elsewhere on the board
/M_DRV_RX: R201.2, R301.2, R401.2; also elsewhere on the board
/M_DRV_TX: R202.1, R302.1, R402.1; also elsewhere on the board
/M_X_DIR: A201.16 (DIR); also elsewhere on the board
/M_X_STEP: A201.15 (STEP); also elsewhere on the board
/M_Y_DIR: A301.16 (DIR); also elsewhere on the board
/M_Y_STEP: A301.15 (STEP); also elsewhere on the board
/M_Z_DIR: A401.16 (DIR); also elsewhere on the board
/M_Z_STEP: A401.15 (STEP); also elsewhere on the board
GND: A201.1 (GND), A201.7 (GND), A301.1 (GND), A301.7 (GND), A401.1 (GND), A401.7 (GND), C201.2, C203.1, C204.1, C205.1, C206.1, C301.2, C303.1, C304.1, C305.1, C306.1, C401.2, C403.1, C404.1, C405.1, C406.1, JP201.1 (A), JP202.1 (A), JP206.1 (A), JP301.1 (A), JP302.1 (A), JP306.1 (A), JP401.1 (A), JP402.1 (A), JP406.1 (A); also elsewhere on the board
unnamed: A201.18 (DIAG), JP203.2 (B)
unnamed: A201.10 (MS1), JP201.2 (C)
unnamed: A201.11 (MS2), JP202.2 (C)
unnamed: A201.12 (MS3/RX), JP204.2 (C)
unnamed: A201.13 (~RESET/TX), JP205.2 (C)
unnamed: A201.14 (~SLEEP/CLK), JP206.2 (C)
unnamed: A301.18 (DIAG), JP303.2 (B)
unnamed: A301.10 (MS1), JP301.2 (C)
unnamed: A301.11 (MS2), JP302.2 (C)
unnamed: A301.12 (MS3/RX), JP304.2 (C)
unnamed: A301.13 (~RESET/TX), JP305.2 (C)
unnamed: A301.14 (~SLEEP/CLK), JP306.2 (C)
unnamed: A401.18 (DIAG), JP403.2 (B)
unnamed: A401.10 (MS1), JP401.2 (C)
unnamed: A401.11 (MS2), JP402.2 (C)
unnamed: A401.12 (MS3/RX), JP404.2 (C)
unnamed: A401.13 (~RESET/TX), JP405.2 (C)
unnamed: A401.14 (~SLEEP/CLK), JP406.2 (C)
unnamed: JP204.1 (A), R201.1
unnamed: JP205.1 (A), R202.2
unnamed: JP304.1 (A), R301.1
unnamed: JP305.1 (A), R302.2
unnamed: JP404.1 (A), R401.1
unnamed: JP405.1 (A), R402.2

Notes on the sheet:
driver protection per TMC2209 datasheet
for A4988: MS1, MS2, MS3 to 3.3V to set microstepping RESET, SLEEP to 3.3V for TMC2209: MS1, MS2 to 3.3V or GND to set UART address RX to MCU RX TX to MCU TX through resistor CLK to GND

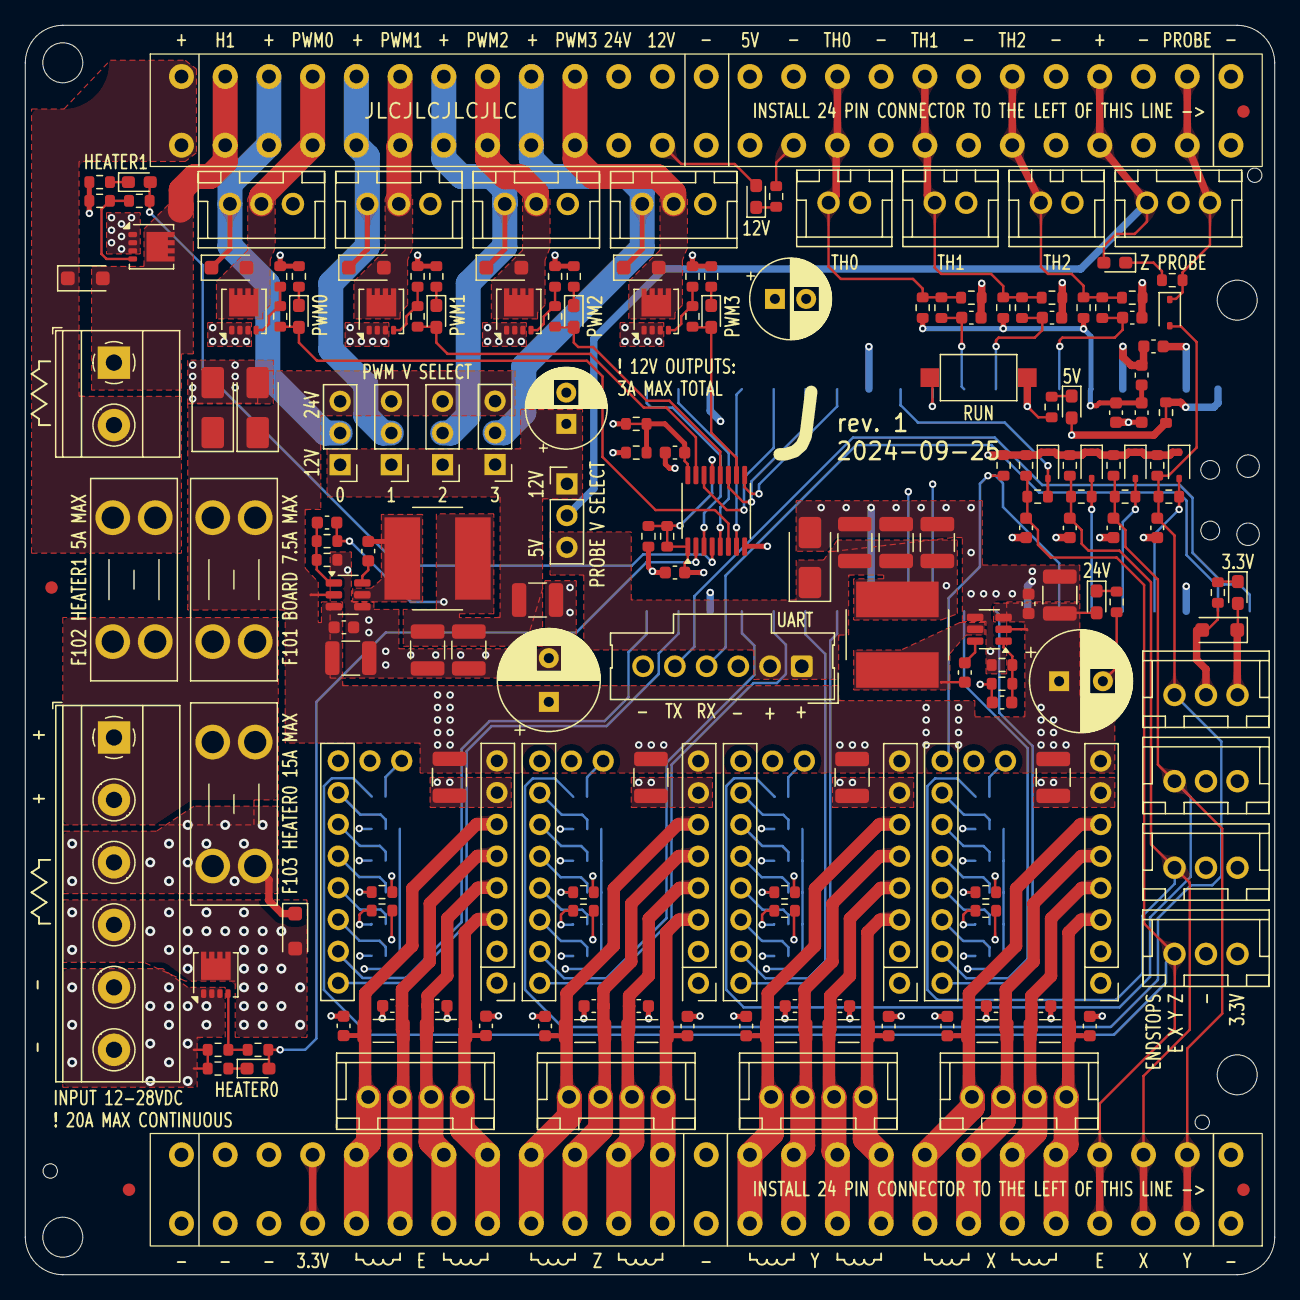
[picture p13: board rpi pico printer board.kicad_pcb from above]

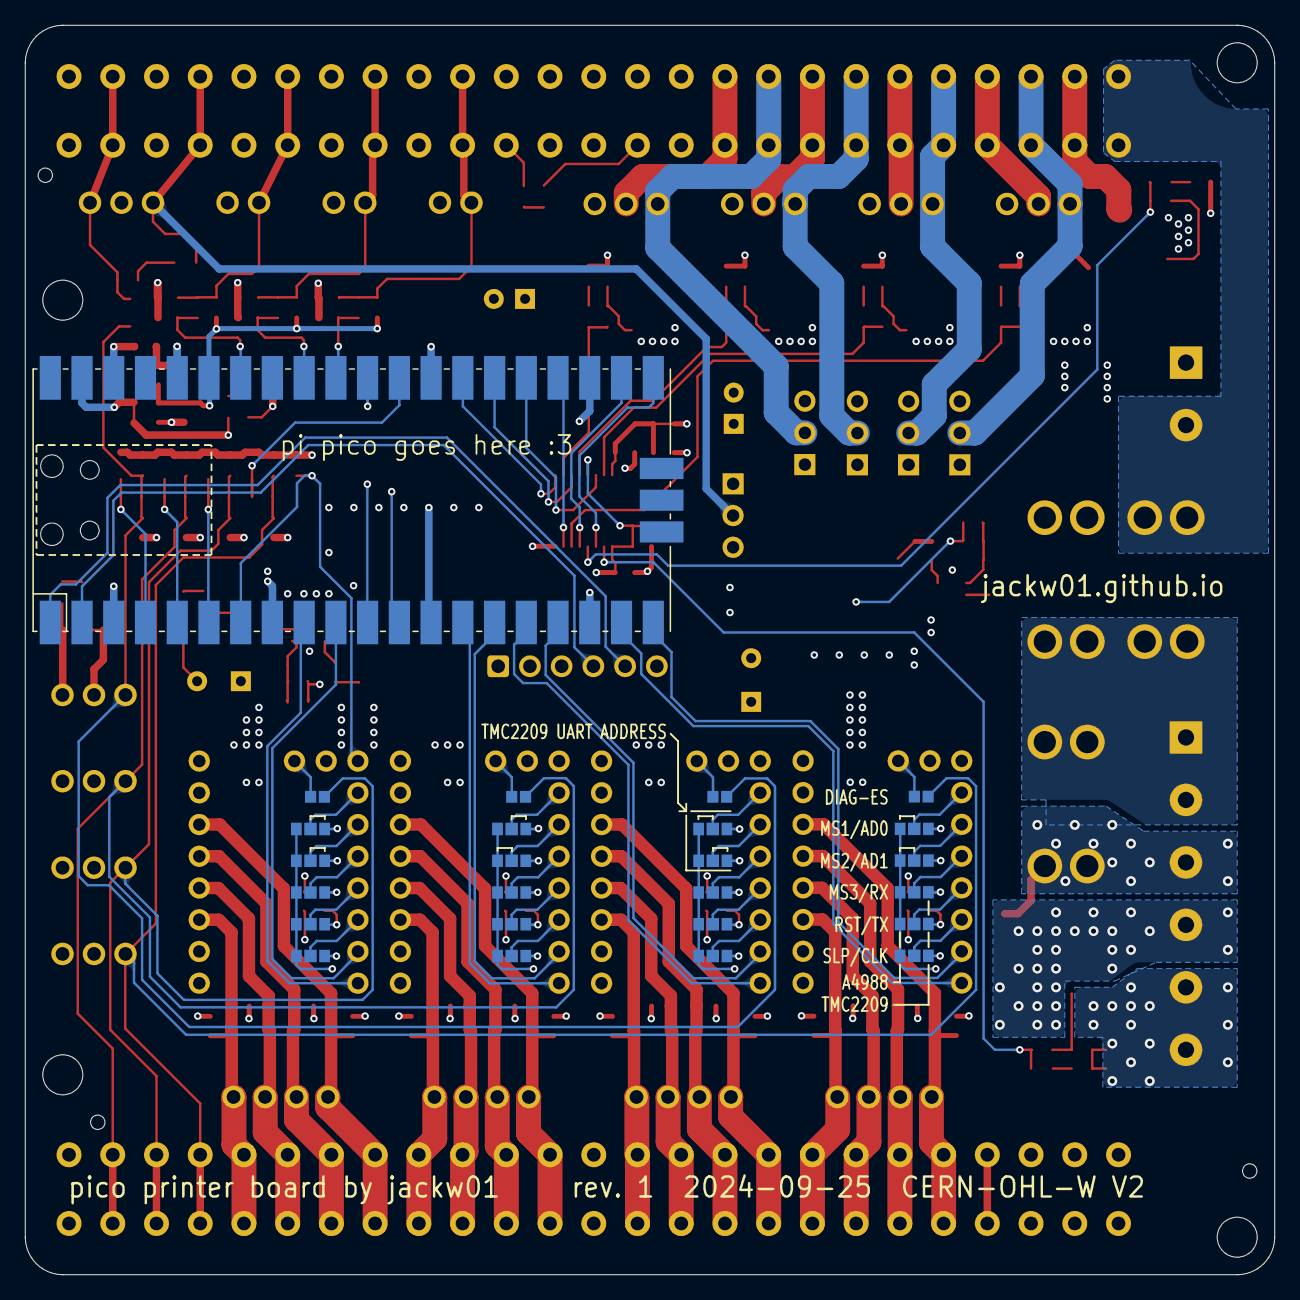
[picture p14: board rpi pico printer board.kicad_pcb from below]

Board: 4 copper layers, 100.0 x 100.0 mm, 224 parts (25 on the bottom side), 135 nets.

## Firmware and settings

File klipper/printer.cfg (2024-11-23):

[include mainsail.cfg]

[mcu]
serial: /dev/ttyAMA0
baud: 250000
restart_method: command

[printer]
kinematics: corexy
max_velocity: 400
max_accel: 18500
minimum_cruise_ratio: 0.12
square_corner_velocity: 8.0
max_z_velocity: 5
max_z_accel: 100

[stepper_x]
step_pin: gpio7
dir_pin: gpio6
enable_pin: !gpio5
microsteps: 16
full_steps_per_rotation: 200
rotation_distance: 40
endstop_pin: ^gpio4
position_endstop: 0
position_min: 0
position_max: 200
homing_speed: 80

[tmc2209 stepper_x]
uart_pin: gpio9
uart_address: 0
#interpolate: False
run_current: 0.700
stealthchop_threshold: 0

[stepper_y]
step_pin: gpio11
dir_pin: gpio10
enable_pin: !gpio5
microsteps: 16
full_steps_per_rotation: 200
rotation_distance: 40
endstop_pin: ^gpio3
position_endstop: 0
position_min: 0
position_max: 180
homing_speed: 80

[tmc2209 stepper_y]
uart_pin: gpio9
uart_address: 2
#interpolate: False
run_current: 0.700
stealthchop_threshold: 0

[stepper_z]
step_pin: gpio13
dir_pin: gpio12
enable_pin: !gpio5
microsteps: 16
full_steps_per_rotation: 200
rotation_distance: 2
endstop_pin: probe:z_virtual_endstop
position_min: -5
position_max: 110

[tmc2209 stepper_z]
uart_pin: gpio9
uart_address: 1
#interpolate: False
run_current: 0.25
stealthchop_threshold: 999999

[probe]
pin: gpio2
x_offset: 16.0
y_offset: -10.0
#z_offset: 1.0
samples: 4
samples_tolerance: 0.075
samples_tolerance_retries: 2

[thermistor NTC100K-B3950]
temperature1: 25
resistance1: 103180
temperature2: 150
resistance2: 1366.2
temperature3: 250
resistance3: 168.6

[extruder]
step_pin: gpio15
dir_pin: gpio14
enable_pin: !gpio5
microsteps: 16
full_steps_per_rotation: 200
rotation_distance: 7.111
nozzle_diameter: 0.600
filament_diameter: 1.750
max_extrude_only_velocity: 40.0
max_extrude_only_accel: 1000.0
heater_pin: gpio17
sensor_type: ATC Semitec 104GT-2
pullup_resistor: 2400
sensor_pin: gpio26
min_extrude_temp: 0
min_temp: 0
max_temp: 280

[tmc2209 extruder]
uart_pin: gpio9
uart_address: 3
#interpolate: False
run_current: 0.6
stealthchop_threshold: 0

[heater_fan heatbreak_cooling_fan]
pin: gpio21

[fan]
pin: gpio19
cycle_time: 0.0001
hardware_pwm: True

[heater_bed]
heater_pin: gpio16
sensor_type: NTC100K-B3950
pullup_resistor: 2400
sensor_pin: gpio27
min_temp: -100
max_temp: 105

[temperature_sensor MCU]
sensor_type: temperature_mcu

[temperature_sensor raspberry pi]
sensor_type: temperature_host

[thermistor NTC47K-B4050]
temperature1: 25
resistance1: 47000
beta: 4050

[temperature_sensor chamber]
sensor_type: NTC47K-B4050
pullup_resistor: 2400
sensor_pin: gpio28
min_temp: -100
max_temp: 100
gcode_id: C

[led main_led]
white_pin: gpio18
initial_WHITE: 1.0

[controller_fan electronics_fan]
pin: gpio20

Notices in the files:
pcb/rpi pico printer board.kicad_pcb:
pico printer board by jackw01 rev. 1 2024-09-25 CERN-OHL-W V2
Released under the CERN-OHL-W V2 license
